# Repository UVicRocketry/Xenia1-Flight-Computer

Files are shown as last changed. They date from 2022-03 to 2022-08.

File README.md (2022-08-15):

# Xenia1-flight-Computer

## Requirements/Imports
To pip install all the necessary imports run
`$ pip install -r requirements.txt`
*Please Update requirements.txt with new imports if you add any*

## Style

- Class names: starting with Pascal Case (capital then camel)
- method: lower snake
- vars: lower snake
- private methods: \_\_ for private methods

Please document your code in the following format:

for classes:

```
  """
  Description of class

  ...

  Attributes
  ----------
  an_attribute(variable)
    Description:
      write description

  Methods
  -------
    Description:
      write description
     Parm:
      parm_name: write point of parameter

  """
```

## Setup and Installation

This system is designed to run on a raspberry pi zero W. To set up clone the repository and run `$ pip install -r requirements.txt`, this will install all necessary dependencies. 

## Design 

The flight computer has two purposes: to store, and to simulate. The system is designed to run on a raspberry pi 0 W running rasbian (Ubuntu ~10). Connected to the pi are multiple senors and devices. The sensor suite contains a adafruit BME280, adafruit LSM..., adafruit Adx..., adafruit ADS... all of which are connected to the pi using 1 I2C bus. A mirco stepper driver is used to control the airbrakes assembly's motor and feedback is given through a potentiometer which is fed into the analog to digital converter. A buzzer is connected to a single GPIO pin on the pi and give auditable feedback to the user. All other electrical components connected to the flight computer can be found in the KiCAD schematic in the source directory.

Due to the nature of embedded systems

Beep codes

## File structure

The Project is broken into two folders a source folder (src) and a sub sensors folders
```
> Xenia1-flight-computer
  > drag_data 
    > cda_no_airbrakes.csv

  > src
    > airbrakes.py
    > suborbit.py
    > rehearsal.py
    > main.py
    > rocketData.py
    > flight_computer.py

  > sensors
    > adx.py
    > bme.py
    > hx711.py
    > lsm.py
```

1. src/airbrakes.py

  Suborbit 

   Computes a the next value to set the airbrakes to position to. Also provides a simple interface for controlling the hardware that Airbrakes uses to  deploy the brakes. It does this through a kalman filter algorithm. Please look at the kalman filter algorithm connected    to the issue X1-AV-6 [](https://github.com/UVicRocketry/Xenia1-flight-Computer/issues/14)

2. src/suboribit.py

3. src/gpioReader.py

   This file reads all the data from the sensor and updates rocketData.

4. src/main.py

   Runs flight computer class

5. src/rocketData.py

   This class holds all the data of the rocket and has functions to manipulate the data.

## Flow of the Program

   <deprecated>
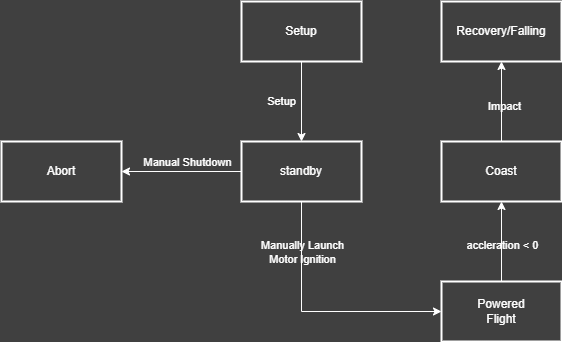
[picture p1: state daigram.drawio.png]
Main State Diagram


Sequence Flow of initial design. This was changed into a class containing different phases 

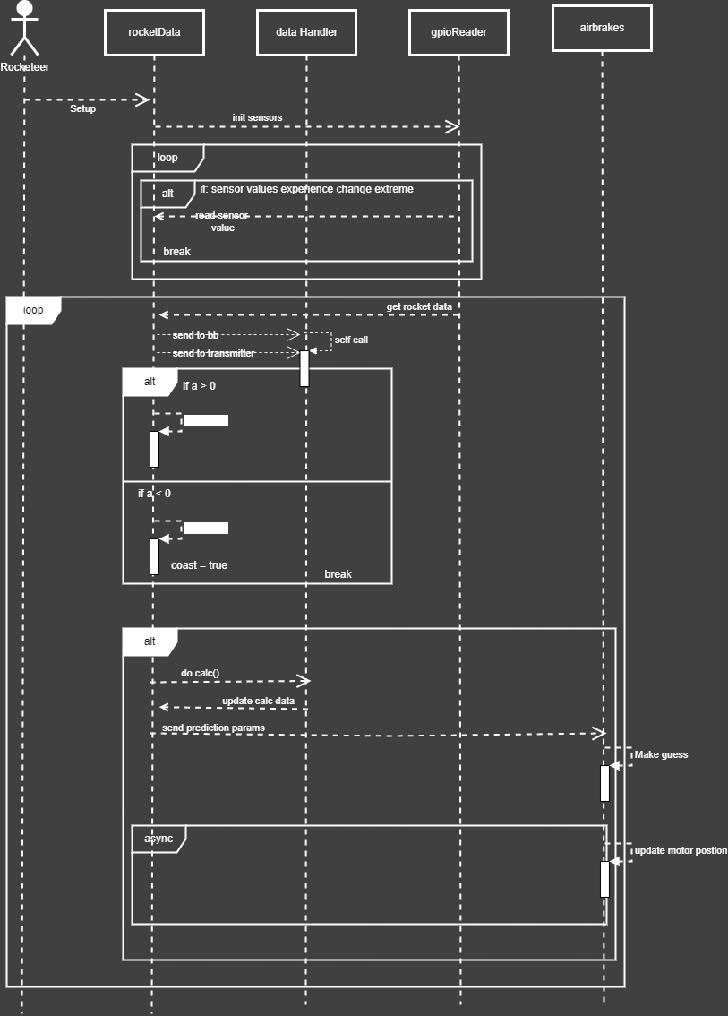
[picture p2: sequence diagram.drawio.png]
Sequence Diagram of main


## Air Brakes

The airbrakes assembly ...

For Xenia-1 we over spec'd our motor 

### Kalman Filter

As an suggestion from the MECH 400 report for airbrakes we explored the Kalman filter option for the predictive element of controlling airbrakes. A Kalman filter as shown in the diagram below predicts new state based on previous state. In the case of airbrakes this is a change in flap opening percentage determined by how the drag produced will impact the final altidute of the flight.   

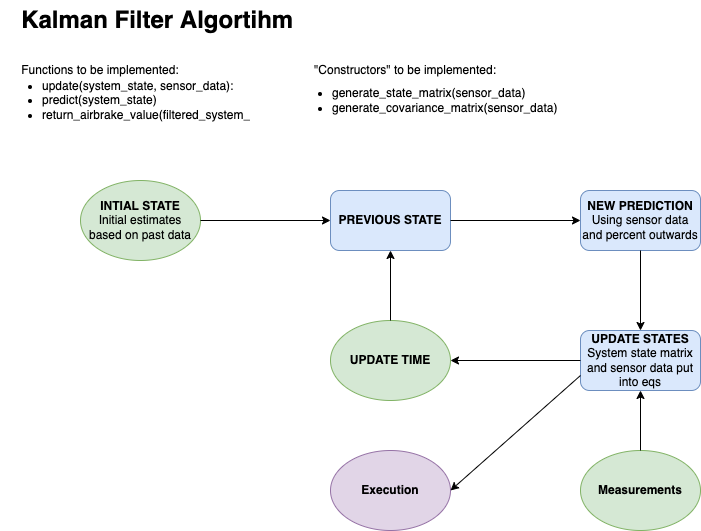
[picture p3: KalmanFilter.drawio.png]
Kalman Filter Image


### Suborbit

## Results and Reflection

After a almost nominal flight Xenia-1 was recovered with somewhat minimal data loss. See (link to post flight analysis) for a post flight analysis break down. Based on these results and barriers during development the following conclusions were made. _A raspberry pi is not a suitable processing unit for a rockets avionics system_. A raspberry pi runs an OS for more general purpose computing, what is needed is a device that only runs processes specific to its purpose. Another problem faced during development was the lack 

Developmentation:

This project should have been designed with proper requirements gathering from all subsystems and all core members involved. In addition a new development strategy was used in the middle of the development. This made the

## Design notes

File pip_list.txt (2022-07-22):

Package                          Version
-------------------------------- ---------
Adafruit-Blinka                  8.0.2
adafruit-circuitpython-ads1x15   2.2.15
adafruit-circuitpython-adxl34x   1.12.3
adafruit-circuitpython-bme280    2.6.13
adafruit-circuitpython-busdevice 5.1.10
adafruit-circuitpython-lsm9ds1   2.1.14
adafruit-circuitpython-typing    1.7.1
Adafruit-PlatformDetect          3.24.1
Adafruit-PureIO                  1.1.9
arandr                           0.1.10
astroid                          2.5.1
asttokens                        2.0.4
automationhat                    0.2.0
beautifulsoup4                   4.9.3
blinker                          1.4
blinkt                           0.1.2
buttonshim                       0.0.2
Cap1xxx                          0.1.3
certifi                          2020.6.20
chardet                          4.0.0
click                            7.1.2
colorama                         0.4.4
colorzero                        1.1
cryptography                     3.3.2
cupshelpers                      1.0
dbus-python                      1.2.16
distro                           1.5.0
docutils                         0.16
drumhat                          0.1.0
envirophat                       1.0.0
ExplorerHAT                      0.4.2
Flask                            1.1.2
fourletterphat                   0.1.0
gpio                             0.3.0
gpiozero                         1.6.2
html5lib                         1.1
idna                             2.10
isort                            5.6.4
itsdangerous                     1.1.0
jedi                             0.18.0
Jinja2                           2.11.3
lazy-object-proxy                0.0.0
logilab-common                   1.8.1
lxml                             4.6.3
machine                          0.0.1
MarkupSafe                       1.1.1
mccabe                           0.6.1
microdotphat                     0.2.1
mote                             0.0.4
motephat                         0.0.3
mypy                             0.812
mypy-extensions                  0.4.3
numpy                            1.19.5
oauthlib                         3.1.0
olefile                          0.46
pantilthat                       0.0.7
parso                            0.8.1
pexpect                          4.8.0
pgzero                           1.2
phatbeat                         0.1.1
pianohat                         0.1.0
piglow                           1.2.5
pigpio                           1.78
Pillow                           8.1.2
pip                              20.3.4
psutil                           5.8.0
pycairo                          1.16.2
pycrypto                         2.6.1
pycups                           2.0.1
pyftdi                           0.54.0
pygame                           1.9.6
Pygments                         2.7.1
PyGObject                        3.38.0
pyinotify                        0.9.6
PyJWT                            1.7.1
pylint                           2.7.2
pyOpenSSL                        20.0.1
pyserial                         3.5b0
pysmbc                           1.0.23
python-apt                       2.2.1
pyusb                            1.2.1
rainbowhat                       0.1.0
reportlab                        3.5.59
requests                         2.25.1
requests-oauthlib                1.0.0
responses                        0.12.1
roman                            2.0.0
rpi-ws281x                       4.3.4
RPi.GPIO                         0.7.0
RTIMULib                         7.2.1
scrollphat                       0.0.7
scrollphathd                     1.2.1
Send2Trash                       1.6.0b1
sense-hat                        2.2.0
setuptools                       52.0.0
simplejson                       3.17.2
six                              1.16.0
skywriter                        0.0.7
sn3218                           1.2.7
soupsieve                        2.2.1
spidev                           3.5
ssh-import-id                    5.10
sysv-ipc                         1.1.0
thonny                           3.3.14
toml                             0.10.1
touchphat                        0.0.1
twython                          3.8.2
typed-ast                        1.4.2
typing-extensions                3.7.4.3
unicornhathd                     0.0.4
urllib3                          1.26.5
webencodings                     0.5.1
Werkzeug                         1.0.1
wheel                            0.34.2
wrapt                            1.12.1

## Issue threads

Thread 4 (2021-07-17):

X1-AV-11 BME and IMU reading

jberryman566, 2021-07-17:
- reading data from sensors

klemie, 2022-02-17:
Needs broken up into smaller issues for each sensor. and have datasheets attached to the new issues

Closed 2022-03-01.

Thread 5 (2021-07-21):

X1-AV-10 Sending Data

jberryman566, 2021-07-21:
- Sending to air brakes  (encoder data )
- black box (Urt)
- ground station (antenna trans) -> in aprs package

The functions for this code can be found in dataHandler.py

klemie, 2022-02-17:
This is now a milestone can close this

Closed 2022-02-17.

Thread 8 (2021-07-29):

X1-AV-9 ADC research

klemie, 2021-07-29:
Research how these work for Rpi Zero W

klemie, 2022-02-17:
Feb 16th Update: I dont think Aila knows this is assigned to her. But this issue is to look into the ADC for the stepper driver.

Closed 2022-02-24.

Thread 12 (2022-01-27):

Wire flight computer

klemie, 2022-01-27:

klemie, 2022-02-17:
Feb 16th update:
@TechGal hasn't done this will do with Alex at the workshop

TechGal, 2022-03-24:
Step 1: mount electronics
step 2: wire (solid core)

apthornwell, 2022-04-02:
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
Followed wiring schematic to wire some things to a breadboard.

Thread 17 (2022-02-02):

X1-AV-5 Fix Holes on Avionics Bay Assembly

klemie, 2022-02-02:
Update the locations of the holes on the avionics bay assembly to accommodate current sensors.

jjderooy, 2022-02-19:
This is complete aside from the mounting for the camera which hasn't been chosen yet.

jjderooy, 2022-02-22:
[Camera](https://www.aliexpress.com/item/1005001597402383.html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) is now chosen and avionics bay holes are corrected.

Closed 2022-02-22.

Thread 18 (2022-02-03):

X1-AV-4 Convert to CSV

klemie, 2022-02-03:
Convert the following JSON object to a CVS:
```
{
  "timestamp": string,
  "bme": {
	  temperature: float,
	  humidity: float,
	  pressure: float
	  },
  "imu":{
	  acceleration: float,
	  magnetometer: float,
	  gyroscope: float,
	  temperature: float
  },
  "strain_gauges":{
	  "strain_one": float,
          "strain_two": float,
	  ....
	  "strain_twelve": float
  },
  "encoders": {
	  "position": float
  }
}
```
You can find more info here: http://142.104.84.19:8080/apps/drawio/9371

Add your solution to src/rocketData.py under the method convert_to_csv()

klemie, 2022-02-03:
This issue blocks sending data

klemie, 2022-02-17:
Feb 16th Update: Sydeny hasn't start yet. Will come to the workshop to get her started.

klemie, 2022-02-24:
Just working through it. But not much progress because of lack of python knowledge

Closed 2022-03-15.

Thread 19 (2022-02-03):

X1-AV-3 Making mocks for BME and IMU

klemie, 2022-02-03:
**Description**
- Mocks are need for all the sensors in order to test how our system reacts to weird flight data

**Acceptance Criteria**
- Create Mocks for IMU and BME
- Print random data using functions already created

**Linked issues**

klemie, 2022-02-17:
Feb 16th update: Met with Connor. Went through testing plan and learned how mocks work.

Closed 2022-03-08.

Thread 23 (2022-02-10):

X1-AV-12 HX711 reading

klemie, 2022-02-10:
Find the data sheet of the HX711 in this [](https://docs.google.com/document/d/1gTJJ3SIZ1-oAkT5Fk1SbSard9b0-FxJ6s4E3crWBEo4/edit) and see if there are any combatiable python libraries if not figure out how we would read the data.

klemie, 2022-02-17:
Feb 16th update: Charlie hasn't been able to get anything done yet. Needs data sheet to look at driver info

jjderooy, 2022-02-19:
This is the datasheet. It includes a C driver that could be rewritten in python if needed. [https://www.digikey.com/htmldatasheets/production/1836471/0/0/1/hx711.html](url)

klemie, 2022-02-24:
- Meet up with @TechGal tomorrow at 4pm

klemie, 2022-03-01:
https://github.com/UVicRocketry/Xenia1-flight-Computer/issues/27#issuecomment-1054649776

klemie, 2022-03-09:
[multi HX711 Arduino](https://github.com/shmulike/HX711-multi)

klemie, 2022-03-17:
mostly the framework is done. Having Troubles changing types. Just let python choose.

Having a hard time reading reading hex from the sensor.

klemie, 2022-03-17:
@PokeyOne will help figure out c conversion

jjderooy, 2022-04-22:
Finished in #56.

Closed 2022-04-22.

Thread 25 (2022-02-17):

X1-AV-13 Make wiring diagram for whole system

krislemie, 2022-02-17:
**Description**
- Create a writing diagram for the flight computer based off of previous diagrams

Previous Diagram: [diagram](https://app.diagrams.net/#G16KAys3ZIa_PrymFaww2CI59HlfeUq78S)
- Note this diagram is very out of date

**Acceptance Criteria**
- Updated Diagram KiCAD schematic uploaded to Xenia1-flight-computer

**Dev Note**
[Write why you decided to do specific wiring arrangement in Pull Request]

klemie, 2022-02-17:
Look at this diagram to see all the components https://drive.google.com/drive/u/0/folders/1lUKZYj5jFLF3oOM159mu564QdC9ljHMy

klemie, 2022-03-01:
Alex is making a diagram in KiCAD

TechGal, 2022-03-03:
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

TechGal, 2022-03-03:
Next steps: put into kicad. and figure out where other sensors go

klemie, 2022-03-17:
Finished 4 sensors in kicad

krislemie, 2022-03-21:
review:
- change Wires to labels
- Harnesses

TechGal, 2022-03-24:
Due by april 1st:

- [ ] Black box - USB connection (two pins Maybe DX and RX)
- [ ] ADC - addafruit 12bit analog to digtail converter (maybe 2 pins)
- [ ] Encoder - @TechGal

TechGal, 2022-05-31:
This last iteration looks really good! Having all the wires run where they will run on the rocket will be very helpful for wiring. If you could label each wire with it's use or protocol, that would be even more helpful. Also, dividing the page using a double line or something so it's very clear where the wiring diagram is and where the full schematic is. It would be really nice if you could edit the RPi schematic object and add the camera port at the bottom, to remove the ambiguity of having that port as it's own separate thing. You can also label the Raven4s with APO -> Drogue, and Main -> Main. These are on the recovery bulkhead, so off to the right of the rest of the schematic (if we look at this as the rocket lying sideways).

Good work, thanks for taking this on.

Closed 2022-06-16.

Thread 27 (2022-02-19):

X1-AV-15 HX711 Testing reading

klemie, 2022-02-19:
**Description**
- Talk to JJ and figure how we are going to read the data from his PCB to the flight computer.

**Acceptance Criteria**
- Software is written that knows how to receive and handle 12 different strain gauge values from 1 hdmi input
- Plan for how to wire HDMI cable to rpi is added to KiCAD schematic that @apthornwell is making in #25

**Dev Notes**

[Write notes on why you choose the wiring that you did. Explain how software works. Document in Pull request description]

cjsquires, 2022-02-28:
This library works for the HX711 (and is in python) https://github.com/gandalf15/HX711/
It the python file of the driver is rather large, but should work. The file also has all the validity checks included, and is very well documented.

If it turns out to be too much for the flight computer to handle, then we could also call the compiled c driver from python.

I can clarify anything that’s confusing to anyone (hopefully)

jjderooy, 2022-03-01:
I had a look at the python lib you linked. It looks pretty good but will need to be modified since we are  using multiple HX711s with a single clock line. Basically the way it works is the flight computer will pulse the clock line, and the HX711 will send data back on the data line. The lib you linked only allows one HX711 (ie one data line) per clock line.

Up to you whether you think it will be easier to modify the library or write your own. After reading through the code, there is a lot of extra error checking and functions which don't really apply to what we're doing like setting the output to kilograms and that sort of thing. Most of these libraries are designed to use HX711s for kitchen weigh scales which is why they have all those features.

Up to you whether you think it will be easier to modify the library or write your own. Alternatively, here is a [multi HX711 Arduino](https://github.com/shmulike/HX711-multi) library that you could convert to python.

TechGal, 2022-03-03:
Move to next sprint.
- converting c++ to python

jjderooy, 2022-04-22:
Finished in #56.

Closed 2022-04-22.

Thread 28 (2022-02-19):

X1-AV-16 Get data from Rpi camera

klemie, 2022-02-19:
**Description**
- The camera we will be using is a raspberry Pi camera look up its data sheet and see if it has a python library.
- Decide weather to save the video in rocketData.py, in a separate file.
- Make sure that it won't slow down our data transfer. If it does decouple it from

**Acceptance Criteria**
- Video is either saved to a video file (That can be sent to black box) or configured in the code and ready to be saved and able to be directly sent to backbox
- See how you would save the camera data to the py and if how python would send it

**Dev Notes**
[for assignee in PR]<write down your thought process when developing this issue>

**Linked issues**
 <If there are any related issues>
Blocked by #33 use this info from this issue to code this issue

TechGal, 2022-03-31:
Will be started later this week.

MaiaPys, 2022-04-01:
Basic video capture script was written but not yet tested due to connectivity issues. Will be tested as soon as possible.

TechGal, 2022-05-11:
@MaiaPys can you please send what you've been working on for the camera? We're hoping to bring together all the updates. Thanks!

Closed 2022-05-18.

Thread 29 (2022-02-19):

X1-AV-17 Write Issues for air brakes plan

klemie, 2022-02-19:
**Description**
Read old repo (python airbrakes), if you are confused on anything talk to conner ebert our team lead.
**Acceptance Criteria**
- Write new issues to break everything up project up into tasks
- Talk to @TechGal and @Kris to make sure they make sense to them

**Dev Notes**
[for assignee in PR]<write down your thought process when developing this issue>

**Linked issues**

klemie, 2022-03-09:
Set a date for the meeting

klemie, 2022-03-10:
Add issues to https://github.com/UVicRocketry/Xenia1-flight-Computer/milestone/3

PokeyOne, 2022-03-17:
# Mateo's Dev Notes

This comment is a work in progress; I'm just writing some notes in a github comment as I work.

Here is a diagram from the "MECH400_FinalReport_Group13.pdf" docment available on GitHub
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

And here is another diagram from the "software in-the-loop testing" section of the same document. Figure 28: "Simulink Model of AACS Control System and Flight Dynamics"
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

*I'm just going to edit this comment as I work through components that this can be broken down into*. After discussing tonight, issues can be created and branches, and then get programming.

## Components/Tasks
Here's a sorta workflow type thing on what needs to be developed
```mermaid
flowchart LR
    Issues[Create Issues] --> sensor[Sensor Data Retrieval in One Object/Struct]
    Issues --> Kalman
    Kalman --> Drag[Drag Optimizer]
    Issues --> Output[What does output look like]
    sensor --> Kalman
    Drag --> Motor
    Kalman -- error data --> Motor[Motor Controller Convert Error into steps]
    Motor --> Output
    sensor --> State["Determine when system is active [1]"]
    State --> Motor
```
[1] See "5.2.6 Active Control Flight Envelope" section of the report.

In the first diagram of this comment, they mention the "State Observer" is where the Kalman stuff would be happening.

**Here are how I'm thinking of breaking this up**:
- [ ] Transform sensor input from raw data to interpretable numbers
- [ ] Make kalman take the input data and output error data.
- [ ] Drag Optimizer (Not sure what this will involve)
- [ ] Convert drag-op and kaman values into flap angles and motor steps
- [ ] Output data back to motor and self.
- [ ] control when system active/not

All stages should include testing of that stage.

## What I'm not Sure on
- Not sure the scope of the "air brakes" plan. Seems like this is less air brakes, and more just flight controller.
- What the drag optimizer 100% does.
- How much of that report we are following exactly and how much is changed in recent development.
- The flight dynamics section of the first graph.
- How are we testing stuff.

klemie, 2022-03-17:
Discuss at meeting

PokeyOne, 2022-03-23:
## Summary of results from meeting on this issue

There is a more detailed summary of the Airbrakes meeting on the Discord under AEROSTRUCTURE in the `# | airbrakes |` channel.

I will be translating a Matlab script we have into python and we will see how well it can predict final altitude of the rocket at different points in flight. If that script works, we may just use that script instead of a full Kalman filter to determine how much we need to deploy airbrakes.

TechGal, 2022-03-24:
other predictive options: TinyML

Closed 2022-04-07.

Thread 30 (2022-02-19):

X1-AV-18 Get[value] Airbrakes Stepper Potentiometer/Encoder

klemie, 2022-02-19:
**Description**
- Get the potentiometer values from the airbrakes and store in rocketData object

**Acceptance Criteria**
- self._data is updated in rocketData.py with the new encoder value (make sure to test this with print statements show screenshots in PR)

**Dev Notes**
[for assignee in PR]<write down your thought process when developing this issue>

jjderooy, 2022-02-19:
The device is just a potentiometer. As you spin it the ADC it is connected to will send a reading of 0-1023 (most likely) to the flight computer GPIO pins. It's just like the VEX potentiometers we used in engr120 if you remember those.

jjderooy, 2022-04-07:
Hopefully mostly fixed in #53 . This at least lays the groundwork for it, though main will still need to actually put the data in rocketData from my understanding. None of the other data have integration with main yet so hopefully this is sufficient?

Closed 2022-05-17.

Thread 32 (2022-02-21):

X1-AV---

TechGal, 2022-02-21:
Design a camera mount to hold a camera against the fuselage of the rocket, without requiring internal access to insert.

jjderooy, 2022-02-22:
I'm not sure how you are organizing things but since this is a mech project rather than software would it make more sense for this to go on openproject?

MorganStuyt, 2022-02-23:
@jjderooy & @TechGal Yes, this task is created in openproject.

jjderooy, 2022-02-23:
Closing this with recommendation from Kris

Closed 2022-02-23.

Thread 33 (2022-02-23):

X1-AV-20 Camera Video storage

klemie, 2022-02-23:
**Description**
- Decide where the camera data will be stored
- decide the rate at the which
- location where it will be stored
- What medium we will be communicating it

**Acceptance Criteria**
- write smaller issues
- decide if we need additional hardware
- what software is needed

**Dev Notes**
[for assignee]<write down your thought process when developing this issue>

**Linked issues**
 <If there are any related issues>

<Add to milestone>
blocked by #28

klemie, 2022-02-24:
- Find the library for python specific camera.
- look on raspberry pi website.
- look at the sensor

Closed 2022-03-21.

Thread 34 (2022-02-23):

X1-AV-21 PID Algorithm

klemie, 2022-02-23:
**Description**
- Create a PID controller to set the kalman output to the set output of the stepper position to
- This is the Kalman filter @TechGal dont think this issue is necessary
(This might be over complicating it @TechGal )

**Acceptance Criteria**
 <Write specifically what is need for this issue to be completed>
- output of PID give a result in an exceptionable range

**Dev Notes**
[for assignee]<write down your thought process when developing this issue>

**Linked issues**
 <If there are any related issues>

jjderooy, 2022-02-25:
I wouldn't bother with a PID controller for the stepper. The flaps don't need to deploy super fast and don't have much inertia either. The nice thing with steppers is that there is no overshoot. I'll close this in a bit unless there was a specific reason you (@klemie/@TechGal) wanted PID that I've missed.

Closed 2022-02-26.

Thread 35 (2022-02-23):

X1-AV-22 Write Recieving data (code + documentation)

klemie, 2022-02-23:
**Description**
- Create pass/fail requirements
- Create script to start the test
- Create test with simulated flight data set and actual sensors

**Acceptance Criteria**
- Tests are verbose and handle all sensors

**Dev Notes**
[for assignee]<write down your thought process when developing this issue>

**Linked issues**
#19

TechGal, 2022-03-31:
Writing a test for the tests, to make sure they work. A sample test.

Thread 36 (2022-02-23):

X1-AV-23 Build simulation flight data set

klemie, 2022-02-23:
# Description
 <Describe what the feature or bug that need to be resolved>
Look at old flight data and create a set of data to be used in testing the system

# Acceptance Criteria

- [ ]  Simulation set should have all sensors, and a time stamp. Follow the same structure shown in Rocketdata.py
- [ ]  simulation set follows the same models an actaul flight
- [ ]  Ask @MorganStuyt  for more info
# Dev Notes
[for assignee]<write down your thought process when developing this issue>

**Linked issues**
Blocks #35

TechGal, 2022-06-09:
data may be weird. Temp readings weird

Closed 2022-11-17.

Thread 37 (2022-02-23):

X1-AV-24 Transmitter Processing

klemie, 2022-02-23:
**Description**
- Convert data into a csv like structure to be sent to the transmitter
- ex: `imu['Imu_t'], imu['imu_h'], imu['imu_p], ..., bme['bme_t], ...`
- Edit `convert_antenna_format` method in rocketData.py

**Acceptance Criteria**
- Formats all of `self._data` into a long array separated by commas similar to #41
- has a maximum of 200 characters -- figure out what values are most import to send to the ground
- Most important parameters will be from BME280, and linear accelleration/velocity from IMU, these will help us develop a picture of the rocket's flight on the ground during flight, and better estimate recovery location.

**Dev Notes**
[for assignee]<write down your thought process when developing this issue in the PR>

**Linked issues**
blocked by #43
#41

Closed 2022-05-11.

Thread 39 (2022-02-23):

X1-AV-25 Airbrakes Stepper/A4988 Control

klemie, 2022-02-23:
**Description**
- @jjderooy

**Acceptance Criteria**
 <Write specifically what is need for this issue to be completed>

**Dev Notes**
[for assignee]<write down your thought process when developing this issue>

**Linked issues**
 <If there are any related issues>

<Add to milestone>

jjderooy, 2022-02-26:
What do you mean by stepper data? They are open loop so there is no feedback. The feedback we get is from the encoder (potentiometer) which already has an issue: #30

jjderooy, 2022-02-26:
Ah gotcha. Stepper control is handled by the A4988s. Logan and I wrote some code for hybrid test stand steppers that can be used. I'll see if I can make a PR for it.

jjderooy, 2022-02-27:
@krislemie  Where should the code for controlling the stepper via a4988s go? It could go either in `main.py` or in `airbrakes.py`. The description for `airbrakes.py` is:
> Computes a the next value to set the airbrakes to position to. It does this through a kalman filter algorithm. Please look at the kalman filter algorithm connected to the issue X1-AV-6

I could update this to include the physical control as well.

Lmk what you think and I'll make a PR.

klemie, 2022-02-27:
Everything should be decoupled from `main.py` so it should be in airbrakes.py a PR would be good

jjderooy, 2022-03-08:
Alright @klemie I'm done with my branch, but I can't test the code until the flight computer is assembled. Would you like a PR anyways?

Closed 2022-03-18.

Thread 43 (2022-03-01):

X1-AV-27 Update rocketData

klemie, 2022-03-01:
**Description**
- Reformate rocketData in rocketData.py to be the actual values from the senors
- For example the IMU is actually called a LSM and has different values then we thought like three

Heres an example:
_Current BME_
```py
   'bme': {
                'yaw': float,
                'pitch': float,
                'roll': float,
                'linear_acceleration': float,
                'linear_velocity': float
    }
```
_More Correct BME_
```py
   'bme': {
                'Temperature': float,
                'Humidity': float,
                'Pressure': float
    }
```
^ look at datasheet for more accurate values.
**Acceptance Criteria**
- Change `self._data` to reflect what the sensors values actually are on the data sheets which you can find in the sending data milestone or datasheets in NC under UVR++ -> Rockets -> Xenia-1 -> Avionics -> Datasheets
- Change Strain Gauges to a list of twelve instead of a dict
- update getters and setter accordingly

**Dev Notes**
[for assignee]<write down your thought process when developing this issue on PR>

**Linked issues**
 <If there are any related issues>

<Add to milestone>

klemie, 2022-03-17:
Wrote down what there suppose to be hasnt started coding yet

Closed 2022-05-17.

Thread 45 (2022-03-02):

X1-AV-28 Threading

klemie, 2022-03-02:
# Description
Have individual threads for Air brakes, data handling. This will decouple the processes from one another and allow air brakes to work paralleled with sending and receiving data.

_Possible problems:_

1. Sending thread could be sending repeat if receiving thread isn't fast enough
[Possible solution]
- Keep sending and receiving data in one thread. Start by receiving then send once all data is collected (I suggest this one)
- Buffer sending thread to only send until receiving thread has collected all the data.
2. air brakes doesn't get updated sensor values in time. Could put the brakes in the wrong position.

Note: use **https://docs.python.org/3/library/threading.html**

1. Initialize threads in `initialize()` phase.
- use `_thread.start_new_thread()`, Takes a function as parameter function this will be the code that the thread executes.
**create 2 threads:**
- one thread for moving air brakes
- one thread for everything else
2. In the `coast_flight` calculate initial suborbit guess
3. In the `coast_flight` phase send airbrakes thread(AB) percentage value and move the motor
- AB thread will move the motor then send a finished flag to the main thread
- Once the main thread receives finished flag it will suborbit again and send that
4.

# Acceptance Criteria
- [ ] Threads handle main processes, Air brakes
- [ ] Checks are made to make sure all data has been received
- [ ] Make sure air brakes thread receives data from data handling thread

**Dev Notes**
[for assignee in PR]<write down your thought process when developing this issue>

**Linked issues**
#22

klemie, 2022-06-02:
Monday: 6pm, threading meeting

TechGal, 2022-06-09:
Moter needs to know length of time on sleep, to determine when and if it should move. Wont need threading, rework airbrakes slighty to get rid of sleep

Closed 2022-06-09.

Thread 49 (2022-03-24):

X1-AV-31 Convert Sub-Orbit from Matlab to Python

ebert-c, 2022-03-24:
**Description**
Sub-Orbit is a matlab program that will allow us to estimate our trajectory in real time.
We will be varying our drag utilizing the airbrakes to hit our target altitude.

We need to convert the Matlab program into Python and integrate it into the flight computer.
It will need to acquire sensor data and use that data to solve for the needed drag coefficient to achieve target altitude.

**Acceptance Criteria**
The Sub-Orbit program is converted to Python from Matlab and is able to receive sensor data from flight computer and output a drag coefficient that is needed to hit target altitude.

**Dev Notes**
[for assignee]<write down your thought process when developing this issue>

**Linked issues**
 <If there are any related issues>

<Add to milestone>

PokeyOne, 2022-04-21:
https://github.com/UVicRocketry/Suborbit-Prediction-Script

PokeyOne, 2022-05-12:
Currently there are three main components of this that need to be done: The atmosphere function, the power phase, and the coast phase.

Currently the atmosphere component is done, the power phase is almost done, and should be done tonight. The coast phase will be very similar to the power phase so this is getting very close to the matlab script.

PokeyOne, 2022-05-12:
Next steps after this is done:
- Test on pi
- Is it fast enough?
- How are we integrating it with the rest?

PokeyOne, 2022-05-18:
Quick update on this for May 18 2022.

I think this is probably closable?

This issue seems to be mostly the conversion of the script.

The script is fully converted over at <https://github.com/UVicRocketry/Suborbit-Prediction-Script> , and most of the stuff left to complete is optimization and evaluation.

Closed 2022-11-17.

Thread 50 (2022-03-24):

X1-AV-32: Control Stepper Motors Based on Needed Drag Coefficient

ebert-c, 2022-03-24:
**Description**
Given a needed drag coefficient, open the flaps controlled by the stepper motor to the position needed to achieve said drag.
A converter between drag coefficient and stepper motor position will be provided by Flight Dynamics.

**Acceptance Criteria**
When given a drag coefficient input, the system can cause the stepper motor to open the flaps to the position that provides that drag coefficient.

**Dev Notes**
[for assignee]<write down your thought process when developing this issue>

**Linked issues**
 <If there are any related issues>

<Add to milestone>

TechGal, 2022-06-09:
Follow up with claire.

TechGal, 2022-06-09:
Need updated drag coefficient list from claire.

Closed 2022-11-17.

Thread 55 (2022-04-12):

X1-AV-33 Refactor HX711 driver for testing

klemie, 2022-04-12:
**Description**
@cjsquires started #54 however this needs to be finished for testing. There were a lot of questions in that code so make sure to follow the reference Arduino driver word closely
**Acceptance Criteria**
- Can read 12 HX711s

**Dev Notes**
[for assignee]<write down your thought process when developing this issue>

**Linked issues**
 <If there are any related issues>

<Add to milestone>

jjderooy, 2022-04-22:
Nothing really needs to be refactored with the driver in #56. It does need to be tested with 12 HX711s on the PCB to be fully sure it works, but I have done quite a bit of testing with breakout boards and it does work fine with 2. I'll close this unless there were other things specifically you wanted to test.

Closed 2022-05-18.

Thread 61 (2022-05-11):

Print new AV bay

TechGal, 2022-05-11:
Description

Acceptance Criteria

Dev Notes
[for assignee]

Linked issues

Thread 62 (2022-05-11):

Wire electronics on AV bay

TechGal, 2022-05-11:
Description

Acceptance Criteria

Dev Notes
[for assignee]

Linked issues

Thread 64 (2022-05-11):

Test programmed RPi to ensure no egregious faults

TechGal, 2022-05-11:
Description

Acceptance Criteria

Dev Notes
[for assignee]

Linked issues

jjderooy, 2022-05-15:
@TechGal this needs a description. After talking with Jenny she has no idea what to do because the issue is so vague. Thanks.

TechGal, 2022-05-17:
Description has been updated, @jjderooy @j7uu

klemie, 2022-05-18:
[@krislemie ]Need an Elec student to wire everything and get everything ready for @j7uu

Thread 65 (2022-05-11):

Check for low-noise filter on ground station

TechGal, 2022-05-11:
Description

Acceptance Criteria

Dev Notes
[for assignee]

Linked issues

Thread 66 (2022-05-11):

Determine gain of transmitting antenna

TechGal, 2022-05-11:
Description

Acceptance Criteria

Dev Notes
[for assignee]

Linked issues

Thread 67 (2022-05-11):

Make feedline for antenna

TechGal, 2022-05-11:
Description

Acceptance Criteria

Dev Notes
[for assignee]

Linked issues

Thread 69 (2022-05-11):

Test ground station with antenna using transmitter

TechGal, 2022-05-11:
Description

Acceptance Criteria

Dev Notes
[for assignee]

Linked issues

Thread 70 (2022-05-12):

X1-AV-34 Test Suborbit script on Pi

krislemie, 2022-05-12:
# Description

Test the speed at which the simulation finish. Test the simulation on 1 thread with another tread running.

## Acceptance Criteria
 <Write specifically what is need for this issue to be completed>

- [x] Speed at which the program runs on the pi is documented
- [ ] How many threads can be ran while program is running
- [ ] Conclusions are made to weather this is a good option for predicting.

# Dev Notes

## From Mateo

***Speed?*** Currently 0.4s

***Thread count?*** This is technically how ever many the OS can manage in memory. But realistically just depends on what else we are running.

***Is it right?*** This needs to be discussed. See comments below.

# Linked Issues

- Over on the script's repo: UVicRocketry/Suborbit-Prediction-Script#4  This has optimization

<Add to milestone>

jjderooy, 2022-05-17:
@PokeyOne can you give an update on where things are at with the optimization you've done?

PokeyOne, 2022-05-17:
The optimization I have done was in UVicRocketry/Suborbit-Prediction-Script#4

This took the execution time on the PI from 54s to about 0.4s

This was on the pi while @jjderooy was doing some very light testing on the pi, and the time does not include loading csv data and sorting the data. The load time shouldn't be included anyway though because it can be done once while the rocket is on the ground, and takes just a few seconds anyway.

The only other thing that I wanted to try off the top of my head was to make the `atmosphere` function inside the script just a LUT to see if that would be faster.

## Is this the right option?

There are a couple factors in whether this is the best option -- mainly accuracy and speed. As far as speed, I think it is reasonable ish. 0.4s ok. It will also take less time as it gets higher, because there is less to predict. I could also make it less precise, but I did already do that. I am hoping that this gets at least a little bit less as things go. Now, in terms of accuracy, it's a bit harder to tell. Currently the script is estimating roughly 12700 ft with full airbrakes and 14400 ft with no airbrakes. I do still need to get exact final mass data and the drag coefficient data will need to be updated with the latest changes to the fins. This is a little bit higher that what ASTOS is saying, but who knows really.

PokeyOne, 2022-05-17:
Also @klemie I updated some of the information in the issue if that is alright. And changed the formatting a little bit if that is alright. I was thinking it could make sense for the headings to be headings in issues, and for the acceptance criteria to be a check list.

Closed 2022-11-17.

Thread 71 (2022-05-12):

X1-AV-35 Python multi threading

krislemie, 2022-05-12:
**Description**
Investigate how to thread in python and write documentation on how to do it.
**Acceptance Criteria**
-
**Dev Notes**
[for assignee]<write down your thought process when developing this issue>

**Linked issues**
 <If there are any related issues>

<Add to milestone>

Closed 2022-05-18.

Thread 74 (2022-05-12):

X1-AV-38 Add HX711 to gpioReader

klemie, 2022-05-12:
**Description**
Use the driver (HX711Multi.py) to get 12 input strain readings put the function in gpioReader

**Acceptance Criteria**
- rocketData its updated with the strain data
- uploaded to pi and tested with testing rig in the rocket room ask @jjderooy or @krislemie how to set it up

**Dev Notes**
[for assignee]<write down your thought process when developing this issue>

**Linked issues**
#56

<Add to milestone>

jjderooy, 2022-05-16:
More context: create an instance of the HX711Multi class and pass it a GPIO pin for the clock, and a list of 12 GPIO pins for data. Then use the build in methods like tare(), isReady() and read() to read strain data from the sensors. There is lots of documentation at the top of the HX711Multi.py file.

krislemie, 2022-05-16:
> More context: create an instance of the HX711Multi class and pass it a GPIO pin for the clock, and a list of 12 GPIO pins for data. Then use the build in methods like tare(), isReady() and read() to read strain data from the sensors. There is lots of documentation at the top of the HX711Multi.py file.

Thanks JJ!

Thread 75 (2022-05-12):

X1-AV-39 Pass Initial values into airbrakes

klemie, 2022-05-12:
**Description**
Initial values are needed inorder to create a prediction.

**Acceptance Criteria**
 <Write specifically what is need for this issue to be completed>

**Dev Notes**
[for assignee]<write down your thought process when developing this issue>

**Linked issues**
 <If there are any related issues>

<Add to milestone>

jjderooy, 2022-05-17:
@PokeyOne is this required for suborbit as it is written currently?

PokeyOne, 2022-05-17:
@klemie What are initial values?

PokeyOne, 2022-05-17:
I think I kinda understand this. There will be some values that the script will need, such as launch altitude. During flight it will also need current altitude, velocity, and acceleration if available. If some of those values are not available directly, using some sort of estimate may be viable. There may be some things that could be done with a temperature and pressure reading on the ground, but that is not currently how it is written.

In summary:

Initial values:
- [ ] launch altitude

During flight
- [ ] altitude
- [ ] velocity
- [ ] acceleration

klemie, 2022-05-18:
I need to fill out this issue better

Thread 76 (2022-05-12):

X1-AV-40 Calc altitude

klemie, 2022-05-12:
**Description**
There are about 3 different ways we can calculate altitude with the sensor data we have. We want to calculate current altitude in those three different ways compare them against eachother and send the result to airbrakes.

create a file called calculations.py and put these 3 calculation in there.
**Acceptance Criteria**

- [ ] multiple calculations of altitude are made
- [ ] a method to compare the calculated values is decided.
- [ ] Error handling checking if compare values are to different

**Dev Notes**
[for assignee]<write down your thought process when developing this issue>

**Linked issues**
 <If there are any related issues>

<Add to milestone>

jjderooy, 2022-05-16:
What sensors are available for calculating altitude?

Closed 2022-07-07.

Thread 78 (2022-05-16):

X1-AV-41 format rocketdata to transmitter state

krislemie, 2022-05-16:
# Description
Work with @TechGal to hack the message for the transmitter. Once figured out how to access the message take the formatted data from RocketData.convert_to_csv_string and format the data to a string and set the message value in the transmitter.

# Acceptance Criteria
 <Write specifically what is need for this issue to be completed>

- [ ] Figure out how to Hack the message field of the transmitter
- [ ] Create a case in csv string function in rocketdata to create a string with only the most import sensor data Char limit of 200c. Do 4 sig figs
- [ ] Write a function to update text field (writtin in send data)
- [ ] Test with actual transmitter to make sure field sends

# Dev Notes
[for assignee]<write down your thought process when developing this issue>

# Linked issues
 <If there are any related issues>
Similar to #37
<Add to milestone>

jjderooy, 2022-05-16:
Can you give some more context of how the transmitter connects? Name of transmitter, and libraries it uses that sort of thing? @TechGal any parameters we need to know about the antenna like character limits, packet frequency etc?

krislemie, 2022-05-16:
char limit is 200 but thats all I know

TechGal, 2022-05-17:
We're using the BigRedBee 70cm APRS [transmitter](https://shop.bigredbee.com/products/70cm-100mw-gps-aprs-transmitter). This transmitter uses a microcontroller which is initially programmed on a Windows computer, including a message which is sent to the ground with the automated GPS data and timestamp. The thing that needs to be determine is whether or not we can use the exposed UART interface to send a new message once / second (the recommended transmission speed). There are some programmers available, and I imagine there are some libraries too, for this microcontroller, but as this specific board is only used in a specific niche, I haven't found any tutorials explicitly discussing this board.

krislemie, 2022-05-19:
150c aprs package. Choose key values from rocketData to send.

krislemie, 2022-05-19:
we should figure out together in CDR

Closed 2022-06-30.

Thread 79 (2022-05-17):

X1-AV-42 add Null checks

klemie, 2022-05-17:
**Description**
For all sensor, any missed value is `null`. Use the last saved value for calculations.

**Acceptance Criteria**
- null checks are added to all sensors read in gpioReader
- `convert_to_cvs_string` in rocketData is updated to send null in the string
- `send_all_data` in dataHandler  is updated to save null properly

**Dev Notes**
[for assignee]<write down your thought process when developing this issue>

**Linked issues**
 <If there are any related issues>

<Add to milestone>

jjderooy, 2022-05-17:
Are you sure writing null is the best option for the data logging? I'm just thinking for when we analyze the data afterwards with matplotlib or excel its gonna be a pain to remove all the nulls. Would it be better to just copy the previous value again instead of null?

PokeyOne, 2022-05-18:
I remember the discussion on this last week, and thinking about it more I think it may actually make more sense to log the previous value.

I think the main argument for logging null would be to preserve the information that we weren't getting anything at that point, but this probably isn't all the important. If we look at the logs after and there is a streak of the exact same value to the 5th decimal place for half the flight we'll be able to tell if nothing was changing. It would also just simplify all the logic and reduce errors within the program. If we just have one variable that stores the previous value then there is one source of truth that is never null. If we start messing with null then we are going to have to check for null on every singe equation and it will get messy real quick.

Also it would just make things easier like JJ said.

Another option would be to just put an empty cell. I know people were saying would make it harder to read last week, but I don't think the CSV is really meant to be read by a human anyway. Most of the time if someone is looking at the data it should just be in some sort of software like excel. I still think I prefer having the previous value over an empty cell, but personally I think an empty cell is better than just writing `null`

Writing null can also be a bit misleading, because it makes it seem like we don't have data. We do have data. It just hasn't been updated that particular cycle.

j7uu, 2022-06-09:
Notes/Discussion From Avionics Meet (2022-06-08)
- Could use last value of the sensor for x amount of time (then enter timeout and use generic value)
- Discussed the merits and pitfalls of using old flight data for generic values (values based on time, values from comparing current sensors to old data, etc)
- Try catch all of main????????

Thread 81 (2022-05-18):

X1-AV-43 Update rocketData with sensor values

klemie, 2022-05-18:
# Description
Currently code has been written to read the sensor data from the IMU and LSM  into print statements. We need to change that to updating a rocketdata instance in main.

1. to do this we will update `__readBME280` and `__readLSM9DS1` by changing the print statements to a single return statement of an object that resembles what the print statements looked like.
eg:
```
print("Temperature: %0.1f C" % self.__bme280.temperature)
print("Humidity: %0.1f %%" % self.__bme280.humidity)
print("Pressure: %0.1f hPa" % self.__bme280.pressure)
```
->
```
return {
     't': self.__bme280.temperature
     ....
}
```
make sure to write fullnames for object keys

2. Create a public varaible of type RocketData (import rocketdata add initialize a new instance)

3. A public function will have to be made to return all updated sensor values. This function will call `__readBme` and `__readLsm` update the public rocketdata variable with the Bme and lsm values

---

These imports were accidentally deleted please add back to the top of gpioReader.
```
import board
import adafruit_lsm9ds1
from adafruit_bme280 import basic as adafruit_bme280
```
Also add imports to requirements.txt (board, adafruit_lsm9ds1, adafruit_bme280 )

---

test your code by running the code with the Mocks and printing out the state of call the public function (should return a rocketdata object). Maybe try running print statement in a for loop in main. Merged version of code will not include this testing code.

# Acceptance Criteria

- [ ]   imports are added in requirement.txt and to the top of gpioReader
- [ ] Screenshot of test results in PR
- [ ] __readBME & __readLSM are change to return objects
- [ ] A public function is created that update a public attribute of type rocketData with the values from `__readBME` & `readLSm`
# Dev Notes
[for assignee]<write down your thought process when developing this issue>

**Linked issues**
 <If there are any related issues>

<Add to milestone>

Closed 2022-06-05.

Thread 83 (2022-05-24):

X1-AV-50 Redo Sensor power Calculation

klemie, 2022-05-24:
# Description
 <Describe what the feature or bug that need to be resolved>
 <Description of the big component that encompasses the issue working on>
 <Depencies, ex. libraries, sensors, hardware, small parts of code youhave to work on>
 <ow to do the things>

Calculations with for sensors are done correctly and checked by other members

# Acceptance Criteria
 <Write specifically what is need for this issue to be completed>

- [x] Power Calculation include all up to date sensor
- [x] Confirm if we have enough power to last +6hr
- [x] Update documentation
- [x] Choose lipos or 9V

# Dev Notes
[for assignee]<write down your thought process when developing this issue>

# Linked issues
 <If there are any related issues>

<Add to milestone>

Closed 2022-06-29.

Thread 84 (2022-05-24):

X1-AV-51 Choose GoNoGo indicator

klemie, 2022-05-24:
# Description
 <Describe what the feature or bug that need to be resolved>
 <Description of the big component that encompasses the issue working on>
 <Depencies, ex. libraries, sensors, hardware, small parts of code youhave to work on>
 <ow to do the things>
 NOTE: if you import anything new add it to the list in `requirements.txt`

Choose a sensor indicator and have a diagram for start up sequence that will trigger the indicator

# Acceptance Criteria
 <Write specifically what is need for this issue to be completed>

- [ ] Choose an indicator. LED vs. Buzzer?
- [ ] Update CAD with indicator
- [ ] Create a flow diagram for the startup sequence
- [ ] Write follow up ticket for software implementation

# Dev Notes
[for assignee]<write down your thought process when developing this issue>

# Linked issues
 <If there are any related issues>

<Add to milestone>

Closed 2022-06-30.

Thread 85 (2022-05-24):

X1-AV-53 Change stepper driver for airbrakes

klemie, 2022-05-24:
# Description

Spec new more reliable stepper driver for airbrakes. @Devon-H knows the right one

# Acceptance Criteria

- [x] Integrate new sensor in cad
- [ ] Learn how to control it with python
- [ ] Implement into `src/airbrakes.py`
- [ ] Test that it works

# Dev Notes

# Linked issues

Devon-H, 2022-05-24:
The stepper motor driver in question is the DRV8825. Here's an amazon [link](https://www.amazon.ca/Baluue-Stepper-Compatible-StepStick-Printer/dp/B08PV6JTK7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) for reference

PokeyOne, 2022-06-29:
I just got assigned to this, but this may or may not already be finished. I know for a fact that I already updated the schematic, but I haven't looked at the code. I'll take a look later today.

If it is already updated, I will still want to test that it works before closing this issue.

Closed 2022-11-17.

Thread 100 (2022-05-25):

X1-AV-58 Velocity Calculations

krislemie, 2022-05-25:
# Description
 <Describe what the feature or bug that need to be resolved>
 <Description of the big component that encompasses the issue working on>
 <Depencies, ex. libraries, sensors, hardware, small parts of code youhave to work on>
 <ow to do the things>
 NOTE: if you import anything new add it to the list in `requirements.txt`

Take the calculated values from #76 and calculate velocities.

Create more functions in `datahandler.py` to calculate multiple velocity using different equations.

# Acceptance Criteria
 <Write specifically what is need for this issue to be completed>

- [ ] Create a list of equations to be used
- [ ] Create corresponding functions to equations
- [ ] Update class documentation explaining what params are need and what equation was used for each function
- [ ] Velocity is calculated

# Dev Notes
[for assignee]<write down your thought process when developing this issue>

# Linked issues
 <If there are any related issues>
blocked by #76
<Add to milestone>

Closed 2022-07-07.

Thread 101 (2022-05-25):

X1-AV-59 Object for storing calculated values [needs AC]

krislemie, 2022-05-25:
# Description
 <Describe what the feature or bug that need to be resolved>
 <Description of the big component that encompasses the issue working on>
 <Depencies, ex. libraries, sensors, hardware, small parts of code youhave to work on>
 <ow to do the things>
 NOTE: if you import anything new add it to the list in `requirements.txt`

Determine weather to create a class to that inherits rocket data properties and stores the calculated attributes or just add on to rocketData.

This object should have altitude, velocity, and acceleration at a specific point in time.

# Acceptance Criteria
 <Write specifically what is need for this issue to be completed>
- [ ]

# Dev Notes
[for assignee]<write down your thought process when developing this issue>

# Linked issues
 <If there are any related issues>

<Add to milestone>

Closed 2022-06-30.

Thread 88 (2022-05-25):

X1-AV-56 standardize apogee prediction and startup

krislemie, 2022-05-25:
# Description
 <Describe what the feature or bug that need to be resolved>
 <Description of the big component that encompasses the issue working on>
 <Depencies, ex. libraries, sensors, hardware, small parts of code you have to work on>
We have a couple different systems on the rocket that need to know apogee and starting launch. Based on the available sensors we need to create a universal way throughout the rocket to know when the launch has happened, and when the rocket has reached apogee.

# Acceptance Criteria
 <Write specifically what is need for this issue to be completed>

- [ ] Gather a list of sensor values available in all three systems (black berry jam, magpi, flight computer) you will have to talk to @cristyro & @Gordon-928 for details.
- [ ] Figure out what sensor values will dictate a launch
- [ ] Create function in `dataHadler.py` to return true when launch is detected
- [ ] Figure out what value will dictate of apogee
- [ ] Create function in `dataHadler.py` to return true when apogee is detected
- [ ] Work with @cristyro & @Gordon-928 to make C++ versions

# Dev Notes
[for assignee]<write down your thought process when developing this issue>

# Linked issues
 <If there are any related issues>

<Add to milestone>

Closed 2022-06-30.

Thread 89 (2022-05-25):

X1-AV-57 Update main.py

krislemie, 2022-05-25:
# Description
 <Describe what the feature or bug that need to be resolved>
 <Description of the big component that encompasses the issue working on>
 <Depencies, ex. libraries, sensors, hardware, small parts of code youhave to work on>
 <ow to do the things>
 NOTE: if you import anything new add it to the list in `requirements.txt`

Follow the sequence diagram in the readme. Make sure to break the logic up into the states as shown in the readme.

1. Setup Phase
- Waiting for input from screw switch (powered off - no code needed)
2. Standby Phase
- Initialize sensors, load suboribit csv, sort csv(will be done in suborbit).
- Then in a loop call read necessary data for
3. Powered Flight Phase

4. Coast Phase

5. Recovery

# Acceptance Criteria
 <Write specifically what is need for this issue to be completed>
Code is written has all these phases
- [ ] Setup up phase - waiting for input from screw switch (powered off - no code needed)
- [ ] Standby Phase - initialize sensors, load suboribit csv, sort csv. Then in a
- [ ]

# Dev Notes
[for assignee]<write down your thought process when developing this issue>

# Linked issues
 <If there are any related issues>

<Add to milestone>

PokeyOne, 2022-05-25:
These are the states of main as I understand them:

```mermaid
stateDiagram-v2
  setup   : Setup
  standby : Standby
  abort   : Abort
  power   : Powered Flight
  coast   : Coast
  reco    : Falling + Recovery
  [*] --> setup     : Turn key
  setup --> standby : All setup tasks are complete
  standby --> abort : System manually turned off
  standby --> power : Ignition detection
  power --> coast   : Burnout detection
  coast --> reco    : Apogee detection
  reco --> [*]      : Manual power off
```

**Note**: Falling and recovery are the same state because at that point it doesn't really matter to flight computer. The flaps should be retracted in both.

PokeyOne, 2022-05-25:
Also @klemie, was just thinking, maybe this issue could be narrowed down to just setting up the main to have a state machine, and then the actual states can be broken up into separate issues. Once things are setup to have states, they can be fairly isolated from each other. This way we can have multiple people working at the same time.

this is a bit of a rough idea that I had:

```mermaid
gantt
  title Main State Machine
  dateFormat YYYY-MM-DD
  excludes weekends
  section Milestones

  Assembly Rehearsal           :milestone, assembly, 2022-06-04, 0d
  Second Assembly Rehearsal    :milestone, aseembly2, 2022-06-11, 0d
  System Acceptance Review     :milestone, acceptance, 2022-06-25, 0d

  section Setup

  Setup state machine logic    :active, init, 2022-05-25, 7d

  section Dependencies

  Ignition detection           :        ignition, 2022-05-25, 7d
  Accel and vel calculations   :        accelvel, 2022-05-25, 7d
  Motor burnout detection      :        burnout, after accelvel, 5d
  Apogee detection             :        apogee, after burnout, 5d

  section States

  Setup                        :        setup, 2022-06-01, 2d
  Standby                      :        standby, after init, 4d
  Powered flight               :        powered, after init, 4d
  Coast flight                 :        coasting, after init, 7d
  Recovery                     :        falling, after standby, 2d
```

Got kinda excited about Gantt charts after the ECE 299 lecture today. Some of the tasks will probably need to be adjusted; this was just an idea that I had and ran with it.

Also these charts are just Mermaid JS charts written as text in the GitHub comment, but I could put these somewhere more permanent at some point.

PokeyOne, 2022-05-26:
I put this into in-progress because PR #99 does at least some of this.

Closed 2022-06-09.

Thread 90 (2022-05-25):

Test USB Type-C to ethernet from fridge (?) with Raspberry Pi

TechGal, 2022-05-25:
# Description
 <Describe what the feature or bug that need to be resolved>
 <Description of the big component that encompasses the issue working on>
 <Depencies, ex. libraries, sensors, hardware, small parts of code youhave to work on>
 <ow to do the things>
 NOTE: if you import anything new add it to the list in `requirements.txt`

Choose a sensor indicator and have a diagram for start up sequence that will trigger the indicator

# Acceptance Criteria
 <Write specifically what is need for this issue to be completed>

- [ ] Retrieve connector from fridge in RR
- [ ] Plug in connector and RPi Zero W
- [ ] See if RPi Zero W can be accessed from laptop
- [ ] Relay instructions to Avionics on how to use

# Dev Notes
[for assignee]<write down your thought process when developing this issue>

# Linked issues
 <If there are any related issues>

<Add to milestone>

Closed 2022-06-15.

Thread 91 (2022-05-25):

Put all hardware deadline updates into OpenProject

TechGal, 2022-05-25:
# Description
 <Describe what the feature or bug that need to be resolved>
 <Description of the big component that encompasses the issue working on>
 <Depencies, ex. libraries, sensors, hardware, small parts of code youhave to work on>
 <ow to do the things>
 NOTE: if you import anything new add it to the list in `requirements.txt`

Choose a sensor indicator and have a diagram for start up sequence that will trigger the indicator

# Acceptance Criteria
 <Write specifically what is need for this issue to be completed>

- [ ] Add command module deadlines
- [ ] Add camera mount deadlines
- [ ] Add wiring deadlines
- [ ] Add ground station deadlines

# Dev Notes
[for assignee]<write down your thought process when developing this issue>

# Linked issues
 <If there are any related issues>

<Add to milestone>

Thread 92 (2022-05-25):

Mount electronics on command module

TechGal, 2022-05-25:
# Description
 <Describe what the feature or bug that need to be resolved>
 <Description of the big component that encompasses the issue working on>
 <Depencies, ex. libraries, sensors, hardware, small parts of code youhave to work on>
 <ow to do the things>
 NOTE: if you import anything new add it to the list in `requirements.txt`

Choose a sensor indicator and have a diagram for start up sequence that will trigger the indicator

# Acceptance Criteria
 <Write specifically what is need for this issue to be completed>

- [ ] Review needed wiring channels with Scott
- [ ] Get CM printed
- [ ] Mount electronics to outside of CM
- [ ] Assemble batteries in CM

# Dev Notes
[for assignee]<write down your thought process when developing this issue>

# Linked issues
 <If there are any related issues>

<Add to milestone>

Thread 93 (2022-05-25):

Spec ground station equipment

TechGal, 2022-05-25:
# Description
 <Describe what the feature or bug that need to be resolved>
 <Description of the big component that encompasses the issue working on>
 <Depencies, ex. libraries, sensors, hardware, small parts of code youhave to work on>
 <ow to do the things>
 NOTE: if you import anything new add it to the list in `requirements.txt`

Choose a sensor indicator and have a diagram for start up sequence that will trigger the indicator

# Acceptance Criteria
 <Write specifically what is need for this issue to be completed>

- [x] Spec LNA, limiter, crossed-yagi antenna for groundstation
- [x] Send list to Levente for feedback
- [x] On response, add to procurement sheet

# Dev Notes
[for assignee]<write down your thought process when developing this issue>

# Linked issues
 <If there are any related issues>

<Add to milestone>

Closed 2022-06-15.

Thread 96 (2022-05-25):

Write testing plans

TechGal, 2022-05-25:
# Description
 <Describe what the feature or bug that need to be resolved>
 <Description of the big component that encompasses the issue working on>
 <Depencies, ex. libraries, sensors, hardware, small parts of code youhave to work on>
 <ow to do the things>
 NOTE: if you import anything new add it to the list in `requirements.txt`

Choose a sensor indicator and have a diagram for start up sequence that will trigger the indicator

# Acceptance Criteria
 <Write specifically what is need for this issue to be completed>

- [ ] Low Power Test
- [ ] Battery Drain Test
- [ ] Avionics / Recovery Integration Test
- [ ] Other tests in the folder

# Dev Notes
[for assignee]<write down your thought process when developing this issue>

# Linked issues
 <If there are any related issues>

<Add to milestone>

macsyd, 2022-06-30:
@TechGal status update? -Kris

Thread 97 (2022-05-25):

How to use ground station as full duplex receiver

TechGal, 2022-05-25:
# Description
 <Describe what the feature or bug that need to be resolved>
 <Description of the big component that encompasses the issue working on>
 <Depencies, ex. libraries, sensors, hardware, small parts of code youhave to work on>
 <ow to do the things>
 NOTE: if you import anything new add it to the list in `requirements.txt`

Choose a sensor indicator and have a diagram for start up sequence that will trigger the indicator

Note that each transmitter will be sending at 1Hz.

# Acceptance Criteria
 <Write specifically what is need for this issue to be completed>

- [ ] How to set up an RTL-SDR to receive two signals at once (full duplex), or monitor two frequencies at once (half duplex)
- [ ] Update software on ground station to include this
- [ ] Test receiving two signals at once

# Dev Notes
[for assignee]<write down your thought process when developing this issue>

# Linked issues
 <If there are any related issues>

<Add to milestone>

Closed 2022-06-30.

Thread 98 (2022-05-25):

Find out if antenna for TeleGPS needs to be bigger

TechGal, 2022-05-25:
# Description
 <Describe what the feature or bug that need to be resolved>
 <Description of the big component that encompasses the issue working on>
 <Depencies, ex. libraries, sensors, hardware, small parts of code youhave to work on>
 <ow to do the things>
 NOTE: if you import anything new add it to the list in `requirements.txt`

Choose a sensor indicator and have a diagram for start up sequence that will trigger the indicator

# Acceptance Criteria
 <Write specifically what is need for this issue to be completed>

- [ ] Find out what ground station setup is using
- [ ] Use Link-Budget spreadsheet to calculate margin for TeleGPS
- [ ] Look into antennas for TeleGPS is needed
- [ ] Talk to Ryan about space in MAGPI for an antenna

# Dev Notes
[for assignee]<write down your thought process when developing this issue>

# Linked issues
 <If there are any related issues>

<Add to milestone>

Closed 2022-06-30.

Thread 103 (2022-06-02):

X1-AV-46 Main: Standy Function

JackCotter, 2022-06-02:
# Description
 The main function is in the standby function until it is launched. Check ONE appropriate sensor in a loop for a large difference in the rockets position indicating launch. Once launch is detected return from the function.
 NOTE: if you import anything new add it to the list in `requirements.txt`

# Acceptance Criteria
 <Write specifically what is need for this issue to be completed>
- [ ]    AC 1

# Dev Notes
[for assignee]<write down your thought process when developing this issue>

# Linked issues
 <If there are any related issues>

<Add to milestone>

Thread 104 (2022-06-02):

X1-AV-47 poweredFlight Function

JackCotter, 2022-06-02:
# Description
This function is used when motor is at full power. Read Sensors, send data to ground station, send data to calculations but do not deploy air brakes. Return from Function when motor is no longer at full power. Detect when motors are no longer at full power or 5 seconds has elapsed.
 NOTE: if you import anything new add it to the list in `requirements.txt`

# Acceptance Criteria
 <Write specifically what is need for this issue to be completed>
- [ ]    AC 1

# Dev Notes
[for assignee]<write down your thought process when developing this issue>

# Linked issues
 <If there are any related issues>

<Add to milestone>

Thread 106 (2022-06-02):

X1-AV-48 coast_flight Function

JackCotter, 2022-06-02:
# Description
 This function is used when rocket is coasting. Read Sensors, send data to ground station, send data to calculations and deploy air brakes as appropriate. Return from Function when rocket hits apogee. Detect when apogee is achieved.
 NOTE: if you import anything new add it to the list in `requirements.txt`

# Acceptance Criteria
 <Write specifically what is need for this issue to be completed>
- [ ]    AC 1

# Dev Notes
[for assignee]<write down your thought process when developing this issue>

# Linked issues
 <If there are any related issues>

<Add to milestone>

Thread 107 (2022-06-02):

X1-AV-49 recovery Function

JackCotter, 2022-06-02:
# Description
 This function is used when rocket is falling (after apogee/y velocity at zero). Read Sensors, send data to ground station, send data to calculations but do not deploy air brakes. Return from Function when rocket stops moving.
 NOTE: if you import anything new add it to the list in `requirements.txt`

# Acceptance Criteria
 <Write specifically what is need for this issue to be completed>
- [ ]    AC 1

# Dev Notes
[for assignee]<write down your thought process when developing this issue>

# Linked issues
 <If there are any related issues>

<Add to milestone>

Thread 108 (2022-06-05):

Update All Files to Use `snake_case` for Variables and Methods.

PokeyOne, 2022-06-05:
# Description

There are many places where we will used `snake_case` in one file and then in another file we will use `lowerCamelCase` and `UpperCamelCase`. We should be just using `snake_case` for all functions and variables. This does not apply to classes.

One example of this is in the `gpioReader.py` file. This should be `gpio_reader.py` and inside all methods should be transformed to snake case as well.

# Acceptance Criteria

- [ ] All variables are snake case
- [ ] All functions are snake case
- [ ] All file names are snake case

# Dev Notes

[for assignee]<write down your thought process when developing this issue>

krislemie, 2022-07-15:
can you pull in the changes from refactor and update accordingly?

PokeyOne, 2022-07-15:
@krislemie Yes, but after assembly rehearsal I think is a better time. This is just a style thing and isn't strictly necessary right now. After assembly rehearsal I'll update the PR and then we can merge it.

Closed 2022-11-17.

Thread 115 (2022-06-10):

Ground Timeout Detection

PokeyOne, 2022-06-10:
# Description

Once the rocket is on the ground we should have a way for the Pi to stop logging information and cleanup active things. This is because the FC will be constantly writing data to BB, and if we were to just shut off FC, it may leave currupted data. Having FC stop logging after a certain amount of time would be ideal.

## How to Detect

There are two main modes of detection that were discussed:
1. General timeout (for example, expected flight time + 10 minutes)
2. Detection of ground (plus a five minute buffer or something)

# Acceptance Criteria

- [ ] Assess whether data curuption would even be a real issue.
- [ ] Assess and decide on the approppriate way to detect this.
- [ ] Implement detection
- [ ] Stop logging data some time after detection.
- [ ] There should be a buffer between detection and stopping logging.
- [ ] There should be a minimum time before it even considers stopping logging.
- [ ] It should **only be able to stop loggin in the recovery state**. It would be very bad if we just stopped logging in the middle of the burn.

PokeyOne, 2022-06-10:
Also something I just thought about:

This might not be super important.

As far as I am aware there are only two types of data being stored:
1. Text (for the csv)
2. Images from cameras

The text can never really be currupted because it should just be appending, and the worst case is an unfinished row in the csv that we can manually edit.

For the images, if we are just storing images every certain period, we may just end up with one unfinished frame. This should leave the rest of the frames just fine.

So have this task might just be making things needlessly complicated.

PokeyOne, 2022-06-10:
Following some discussion in the Discord:

This is probably still worth it in some form.

Another way we could do this is through detecting when the transmitter stops responding and then stop. This way we could just shut down the transmitter and then wait five seconds before turning off the pi.

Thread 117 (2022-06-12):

X1-AV-61 Update GPIO pins in sensor classses

klemie, 2022-06-12:
# Description
 <Describe what the feature or bug that need to be resolved>
 <Description of the big component that encompasses the issue working on>
 <Depencies, ex. libraries, sensors, hardware, small parts of code youhave to work on>
 <ow to do the things>

We need to set up all the pins that sensors are connected to in their sensor classes. Go to the wiring diagram on Alex's branch and follow the labels to the pi. Use CONSTANTS for the pins at the top of the files.

# Acceptance Criteria
 <Write specifically what is need for this issue to be completed>

- [ ] bme.py, lsm.py, adx.py, hx711s.py are updated with GPIO pins initialized
- [ ] GPIO is sourced from Alexs wiring diagram

# Dev Notes
[for assignee]<write down your thought process when developing this issue>

# Linked issues
 <If there are any related issues>

<Add to milestone>

krislemie, 2022-06-29:
Sensors do this automatically. Might have to fix something with bus addressing

Closed 2022-06-30.

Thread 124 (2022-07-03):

Remove tare() function from HX711-Multi.py

jjderooy, 2022-07-03:
# Description
Realized the tare() function is necessary since we can tare based on the on the rail strain values after the flight is over. This removes our numpy dependency (at least from this file).

# Acceptance Criteria
- [ ]    Delete the tare() function and fix any of it's integrations into the other functions.

# Dev Notes
[for assignee]<write down your thought process when developing this issue>

# Linked issues
 <If there are any related issues>

<Add to milestone>

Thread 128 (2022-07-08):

X1-AV-64 Refactor Sensor Classes to Simply

JackCotter, 2022-07-08:
# Description

hrmm

# Acceptance Criteria
 <Write specifically what is need for this issue to be completed>
- [ ]    AC 1

# Dev Notes
[for assignee]<write down your thought process when developing this issue>

# Linked issues
 <If there are any related issues>

<Add to milestone>

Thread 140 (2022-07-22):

X1-AV-67 Write camera.py

JackCotter, 2022-07-22:
# Description
 <Describe what the feature or bug that need to be resolved>
 <Description of the big component that encompasses the issue working on>
 <Depencies, ex. libraries, sensors, hardware, small parts of code youhave to work on>
 <ow to do the things>
 NOTE: if you import anything new add it to the list in `requirements.txt`

# Acceptance Criteria
 <Write specifically what is need for this issue to be completed>
- [ ]    AC 1

# Dev Notes
[for assignee]<write down your thought process when developing this issue>

# Linked issues
 <If there are any related issues>

<Add to milestone>

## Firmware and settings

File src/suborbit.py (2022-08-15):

import csv
import numpy
import functools
from collections import namedtuple

# Rocket mass in kg, including the fuel grain
ROCKET_WET_MASS = 20.493
FUEL_GRAIN_MASS = 3.423
ROCKET_DRY_MASS = ROCKET_WET_MASS - FUEL_GRAIN_MASS

# TODO: Is this needed anywhere
ROCKET_AREA = 0.011050733

# Data type for storing elements of rocket position
#
# Seems roughly equivalent a struct in other compiled languages (i.e. C, Rust)
RocketPosition = namedtuple("RocketPosition", [
    "altitude", "velocity", "acceleration"
])

# TODO: !MC - Possibly rename this because there is a class in the Xenia stuff
#       that has the same name. Maybe call this FlightData??
class DragData:
    """Storage of rocket information to be used for predictions.

    Fields
    ------
    cd_no_airbrakes_data:
      Drag coefficient with no airbrakes. Each element of the array is an array
      of mach number, cd area with power on, and cd area with no power.
    """

    def __init__(self, cd_no_airbrakes_path):
        """Initialize a new DragData object with the data specified.

        Panics
        ------
        The method will exit with status code 1 if any of the files could
        not be opened succesfully.

        Params
        ------
        cd_no_airbrakes_path:
            The path relative to program execution to the csv data for the
            coefficient of drag without airbrakes.
        """

        self.cd_no_airbrakes_data = []

        try:
            # Open the file.
            cd_no_airbrakes_file = open(cd_no_airbrakes_path, newline = '')

            cd_no_airbrakes_csv_reader = csv.reader(cd_no_airbrakes_file)
            # Store the data.
            for (i, row) in enumerate(cd_no_airbrakes_csv_reader):
                if i == 0:
                    continue
                self.cd_no_airbrakes_data.append(numpy.array(row).astype(float))

            # Close the files.
            cd_no_airbrakes_file.close()
        except:
            print("Couldn't open file")
            exit(1)

        self.cd_no_airbrakes_data.sort(key=functools.cmp_to_key(compare_drag_row))


def compare_drag_row(a, b):
    return a[0] - b[0]


def flap_area_from_degrees(degrees):
    """Get the flap area in meters squared from the degrees of opening.

    Degrees is the angle from closed in degrees, and area is in meters squared.
    """
    return -4.0e-7 * (degrees**2) + 9e-5 * degrees + 5e-5


def find_drag_coefficient(data, mach_number):
    """Binary search drag coefficient data.

    This could be accomplished with the bisect.bisect_left method in
    Python 3.10, but the Pi can only run 3.7 unless we complile from source.

    Params
    ------
    data:
      This should either be the cd_no_airbrakes_data array in a DragData object.

    mach_number:
      The desired mach number to look for.
    """
    if len(data) == 0:
        return [mach_number, 0.0, 0.0]

    if len(data) == 1:
        return data[0]

    index = int(len(data)/2)
    start = 0
    end = len(data)

    while end - start > 2:
        if data[index][0] < mach_number:
            start = index
        else:
            end = index

        index = int((end - start) / 2) + start

    return data[start]


def atmosphere(altitude):
    """Calculate the speed of sound and air density at a given altitude.

    This function is taken from atmosisa and atmoslapse functions in matlab,
    which are based on the International Standard Atmospher Model. This also
    simplifies the calculations by using standard atmospheric values. These
    values were also used in the Matlab Library.

    Params
    ------
    altitude:
      The altitude in meters.

    Returns
    -------
    The return value is a tuple[float, float]
    Where the first float is the speed of sound in meters per second,
    and the second float is the air density in kilograms per meter cubed.
    """
    # Scalar acceleration due to gravity in metere per second squared.
    gravity = 9.80665
    # Scalar specific heat ratio
    specific_heat_ratio = 1.4
    # Scalar characteristic gas constant joules per kilogram-kelvin.
    characteristic_gas_constant = 287.0531
    # Scalar lapse rate in kelvin per meter.
    lapse_rate = 0.0065
    # Height of troposphere in meters.
    troposphere_height = 11000
    # Height of tropopause in meters.
    tropopause_height = 20000
    # Air density at mean sea level in kilograms per meter cubed.
    air_density_at_sea_level = 1.225
    # Static pressure at mean sea level in pascal.
    static_pressure_at_sea_level = 101325
    # TODO: !MC - We may need this to be variable for launch day??
    # Scalar absolute temperature at mean sea level in kelvin.
    absolute_temperature_at_sea_level = 288.15

    # TODO: !MC - Replace these in the equations with the full names. These just
    #       happen to be what the matlab script used.
    h = altitude
    g = gravity
    gamma = specific_heat_ratio
    r = characteristic_gas_constant
    l = lapse_rate
    hts = troposphere_height
    htp = tropopause_height
    rho0 = air_density_at_sea_level
    p0 = static_pressure_at_sea_level
    t0 = absolute_temperature_at_sea_level
    h0 = 0

    if h > htp:
        h = htp

    if h < h0:
        h = h0

    # TODO: min function??
    h_tmp = h
    if h > hts:
        h_tmp = hts

    t = t0 - l * h_tmp

    expon = 1
    if h > hts:
        expon = numpy.exp((g / (r * t)) * (hts - h))

    a = numpy.sqrt(t * gamma * r)

    theta = t / t0

    rho = rho0 * pow(theta, (g / (l*r)) - 1.0) * expon

    return (a, rho)


def grav(alt):
    """Calculate gravity at a certain altitude in meters.

    Params
    ------
    alt:
      Altitude in meters.
    """
    # This gravity was just set based on an only estimator for
    # Cochrane Ontario, using a base elevation of 275m for ground level,
    # adding 5000ft for the middle of flight ish. The idea was that this
    # would be faster, but the benefits are negligable.
    return 9.805#(6.67408e-11 * 5.972e24) / pow((6.371e6 + alt), 2)


class Suborbit:
    def __init__(self):
        self.data = DragData("/home/pi/Xenia1-flight-Computer/drag_data/cda_no_airbrakes.csv")
        self.previous_sim = None


    def calc_airbrakes_position(self, current_alt, estimated_alt, current_brakes):
        apogee_alt_diff = estimated_alt - 3048
        current_alt_diff = current_alt - 3048

        movement = 10.0
        if abs(apogee_alt_diff < 1000):
            movement *= 0.5
        
        if abs(apogee_alt_diff < 500):
            movement *= 0.5

        if abs(apogee_alt_diff < 100):
            movement *= 0.5

        movement *= apogee_alt_diff / abs(apogee_alt_diff)

        result = current_brakes + movement

        if result < 0:
            return 0.0
        elif result > 100:
            return 100.0

    def run(self, alt, vel, accel, airbrakes, dry_mass = ROCKET_DRY_MASS):
        """
        Calculate the height of apogee and how long until apogee.

        Params
        ------
        alt:
            Altitude in meters
        vel:
            Velocity in meters per second
        accel:
            Acceleration in meters per second per second
        airbrakes:
            The amount of airbrakes currently deployed. For example, 0.8 would
            mean that airbrakes are 80% deployed.


        Returns
        -------
        The value returned with be of type (float, float), containing the max
        altitude in meters, and the time until the rocket gets there.
        """
        if not ((not alt is None) and (not vel is None) and (not accel is None)):
            if self.previous_sim:
                return self.previous_sim
            else:
                return self.run(0, 0, 0, 0.0)

        initial_position = RocketPosition(alt, vel, accel)

        # Intentionally ignoring any sort of power phase because not needed.

        # This will return (float, float)
        res = self.__coast(initial_position, dry_mass, airbrakes, 0.0, self.data)

        self.previous_sim = res

        return res

    def __coast(
            self,
            initial_position,
            mass,
            airbrakes_amount,
            time,
            data
    ):
        """Rocket coasting to apogee after motor shut down.

        Params
        ------
        initial_position:
            The position of the rocket at the start of the coast phase.
        mass:
            The mass of the rocket during the coast phase.
        airbrakes_amount:
            The ratio of airbrakes to no airbrakes as a decimal. For example,
            0.8 would mean airbrakes 80% out.
        data:
            The data object that contains the drag coefficient LUT.
        """
        # TODO: !MC - Remove the data parameter and use self.data

        # Fixed dt because we are only ever using one data set.
        time_delta = 0.1
        last_position = initial_position

        while last_position.velocity > 0:

            # TODO: Use better variables than a and rho
            #       speed_of_sound and air_density
            # Calculate atmospheric conditions
            (a, rho) = atmosphere(last_position.altitude)

            # Calculate drag force.
            m_temp = last_position.velocity / a
            # TODO: !MC - When running the actual rocket, this will have to do some
            #       mixing between the airbrakes and no_airbrakes data based on the
            #       current_airbrakes position.

            # Index of one is the power off CdA
            cda_no_airbrake = find_drag_coefficient(
                data.cd_no_airbrakes_data,
                m_temp
            )[1]

            # TODO: 1.1 is constant for flap Cd, 80.0 should be the max angle of airbrakes.
            #       These should be global constants, and the max angle should be adjusted.
            # TODO: Actually just change the airbrakes_amount to airbrakes_degrees. Easier that way. And I think easier for FC to compute.
            drag_area_coefficient = cda_no_airbrake + 1.1 * flap_area_from_degrees(airbrakes_amount * 80.0)
            drag = drag_area_coefficient * 0.5 * rho * pow(last_position.velocity, 2)

            g = grav(last_position.altitude)

            accel = -drag / mass - g
            vel = last_position.acceleration * time_delta + last_position.velocity
            alt = last_position.velocity * time_delta + ((last_position.acceleration * pow(time_delta, 2)) / 2) + last_position.altitude

            # Check if we have hit the ground (Hopefully not!)
            if alt < initial_position.altitude:
                accel = 0
                vel = 0
                alt = initial_position.altitude

            last_position = RocketPosition(alt, vel, accel)

            # I'm not sure why it is going for plus one and plus two, but that was
            # what the original script did.
            time += time_delta

        return (last_position.altitude, time)


################################################################################
# Tests
#
# TODO: Move tests to own file
################################################################################

def test_data_loading():
    data = DragData("drag_data/cda_no_airbrakes.csv")

def test_running():
    so = Suborbit()

    (max_alt, max_time) = so.run(552.7, 352.45, -9.8, 0.0)
    (min_alt, min_time) = so.run(552.7, 352.45, -9.8, 1.0)
    print("max: alt =", max_alt, "time =", max_time)
    print("min: alt =", min_alt, "time =", min_time)

def run_tests():
    test_data_loading()
    test_running()
    print("All tests passed!")

if __name__ == "__main__":
    run_tests()

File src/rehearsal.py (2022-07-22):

# Rehearsal script
#
# This script is meant to be run during the assembly rehearsal instead of main
# that will do the things with the sensors.
#
# MOST LOGIC SHOULD BE IN THE MAIN CODE. In theory, this should be only calling
# functions and controlling the flow.

import board
import math
import csv
import time
from airbrakes import Airbrakes
from adafruit_bme280 import basic as adafruit_bme280
import adafruit_lsm9ds1
import adafruit_adxl34x
import RPi.GPIO as GPIO
import busio
from sensors.bme import Bme
from sensors.lsm import Lsm
from sensors.adx import Adx
from sensors.hx711s import Hx711
from flight_computer import FlightComputer as FC

i2c = board.I2C()

local_time = time.localtime()

lsm = None
adx = None
bme = None
flight_computer = None

def startup():
    """Initialize all the things"""
    global flight_computer
    flight_computer = FC()
    config_sensors()


def init_airbrakes():
    """This should initialize the airbrakes stepper motor and open and close airbrakes

    The main driver for the airbrakes should automatically do this upon
    initialization.

    Don't stand next to the airbrakes at this point.
    """
    airbrakes = Airbrakes(False, 8, 4, 7)
    # This will wave at the fans (move the brakes in and out)
    airbrakes.calibrate()
    airbrakes.deployBrakes(0)


def read_hx711s():
    """Basically like zeroing a scale, but with the strain gauges"""
    if strain_gauges.isReady():
        strain_gauges.readRaw()

def config_sensors():
    """Test readings from sensors, returns true if all sensors read something"""
    global bme
    global i2c
    global lsm
    global adx
    global strain_gauges

    lsm = Lsm(i2c)
    adx = Adx(i2c)
    bme = Bme(i2c)
    strain_gauges = Hx711()

    lsm.refresh()
    adx.refresh()
    bme.refresh()

    print("bme Temperature:", bme.temperature)
    print("Lsm Temperatrue:", lsm.temperature)
    print("Lsm Acceleration:", lsm.acceleration)
    print("Adx Acceleration:",  adx.acceleration)


def gather_data():
    """
    Collect data once and return. Data in blackbox will show up as a csv

    Order of collected data:
        Timestamp
        [bme]: temperature, humidity, pressure, altitude
        [lsm]: acceleration: x, y, z; magnometer: x, y, z; gyroscope: x, y, z, temperature
        [adx]: acceleration: x, y, z
    """
    global lsm
    global bme
    global adx

    lsm.refresh()
    bme.refresh()
    adx.refresh()

    lsm_acc_x, lsm_acc_y, lsm_acc_z = lsm.acceleration
    lsm_mag_x, lsm_mag_y, lsm_mag_z = lsm.magnetic
    lsm_gyro_x, lsm_gyro_y, lsm_gyro_z = lsm.gyro
    lsm_temp = lsm.temperature

    bme_temp = bme.temperature
    bme_alt = bme.altitude
    bme_hum = bme.humidity
    bme_press = bme.pressure

    adx_acc_x, adx_acc_y, adx_acc_z = adx.acceleration
    timestamp = time.strftime("%H:%M,%S", local_time)

    return [
        timestamp,
        bme_temp,
        bme_hum,
        bme_press,
        bme_alt,
        lsm_acc_x,
        lsm_acc_y,
        lsm_acc_z,
        lsm_mag_x,
        lsm_mag_y,
        lsm_mag_z,
        lsm_gyro_x,
        lsm_gyro_y,
        lsm_gyro_z,
        lsm_temp,
        adx_acc_x,
        adx_acc_y,
        adx_acc_z
    ]

def send_to_black_box(data, f):
    writer = csv.writer(f)
    writer.writerow(data)


def rehearsal():
    global flight_computer
    startup()
    # one minute of reading
    time_out = time.time() + 60
    f = open('/media/pi/XENIA-1_BB/rehearsal.txt', 'a')
    send_to_black_box("Here is the order of values: \n timestamp, bme_temp, bme_hum, bme_press, bme_alt, lsm_acc_x, lsm_acc_y, lsm_acc_z, lsm_mag_x, lsm_mag_y, lsm_mag_z, lsm_gyro_x, lsm_gyro_y, lsm_gyro_z, lsm_temp, adx_acc_x, adx_acc_y, adx_acc_z \n\n", f)
    while True:
        if time.time() > time_out:
            break
        data = gather_data()
        send_to_black_box(data, f)

    f.close()

    flight_computer.beep()
    flight_computer.beep()

if __name__ == "__main__":
    rehearsal()

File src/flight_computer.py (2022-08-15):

import board

import time
from airbrakes import Airbrakes
import RPi.GPIO as GPIO
import busio
from rocketData import RocketData
import numpy as np
import suborbit

from HX711Multi import HX711_Multi

# Gees required to exit standby. This G load must be sustained for a certain time
# TODO CHECK THESE WITH CLAIRE AND FIGURE OUT IF THEY ARE IN G or m/s
STANDBY_ACCELERATION_THRESHOLD = 3*9.81
POWERED_FLIGHT_EXIT_THRESHOLD = -9

# Motor burn time is 3s according to data sheet.
POWERED_TIMEOUT = 3*1.15

#  From flight dynamics.
COAST_TIMEOUT = 300

# Under parachute from max apogee of 14000ft, the rocket takes 310s to descend.
RECOVERY_TIMEOUT = 310*1.5
BUZZ_PIN = 21

# BLACKBOX_FILEPATH = "/media/pi/black_box"
BLACKBOX_FILEPATH = "/media/black_box/flight_data_" + str(time.strftime("%H-%M-%S")) + ".txt"

def mach(n):
    return 339.0 * n

class FlightComputer:
    def __init__(self):
        print("initting the FC")
        self.rocket_data = RocketData()

        print("Attempting to open file")
        self.black_box = open(BLACKBOX_FILEPATH , "a+")


        print("Suborbit")
        self.suborbit = suborbit.Suborbit()

        print("Airbrakes")
        self.airbrakes = Airbrakes(False, 8, 4, 7)

        print("Startup")
        self.startup()
        print("Seatbelt sign is on (FC is initialized)")


    def startup(self):
        """Initialize all the things"""

        print("Sensor roll call\n  buzzer")
        self.__config_buzzer()
        self.beep(duration = 1) 
        time.sleep(5)

        if self.rocket_data.lsm_sensor_ready():
            # lsm sensors read correctly
            print("  lsm init successfully")
        else:
            self.beep(count = 1)
            time.sleep(3.0)
            print("  lsm failed to init")

        if self.rocket_data.bme_sensor_ready():
            # bme sensors read correctly
            print("  bme init successfully")
        else:
            self.beep(count = 2)
            time.sleep(3.0)
            print("  bme failed to init")

        if self.rocket_data.adx_sensor_ready():
            # adx sensors read correctly
            print("  adx init successfully")
        else:
            self.beep(count = 3)
            time.sleep(3.0)
            print("  adx failed to init")

        if self.airbrakes.calibrate():
            print("  airbrakes init successfully")
        else:
            self.beep(count = 4)
            time.sleep(3.0)
            print("  airbrakes failed to init")
        self.airbrakes.deployBrakes(0)
        self.beep(duration = 1) 
        time.sleep(5)

    def __config_buzzer(self):
        GPIO.setup(BUZZ_PIN, GPIO.OUT)


    def beep(self, duration = 0.2, count = 1):
        """
        This method should buzz the buzzer. Different durations mean different
        things, default of 0.2 indicate success
        """
        print("beeping", count, "times, for", duration, "seconds")
        
        return 

        for i in range(count):
            if not i is 0:
                time.sleep(duration)
            

            GPIO.output(BUZZ_PIN, GPIO.HIGH)
            time.sleep(duration)
            GPIO.output(BUZZ_PIN, GPIO.LOW)


    def vec_len(v):
        return np.sqrt(np.dot(v, v))


    def __standby(self):
        self.airbrakes.sleep()
        while True:
            print("Stnadby")
            self.rocket_data.refresh()
            self.rocket_data.send_to_black_box(self.black_box)
            current_accel = FlightComputer.vec_len(self.rocket_data.current_acceleration)
            if current_accel < STANDBY_ACCELERATION_THRESHOLD:
                timer = time.time()
                if abs(timer - time.time()) > 1:
                    break


    def __powered_flight(self):
        time_at_start = time.time()

        while True:
            print("Powered Flight")
            self.rocket_data.refresh()
            self.rocket_data.send_to_black_box(self.black_box)
            if time.time() > (time_at_start + POWERED_TIMEOUT) or self.rocket_data.current_acceleration < POWERED_FLIGHT_EXIT_THRESHOLD:
                break


    def __coast_flight(self):
        time_at_start = time.time()
        self.airbrakes.wake()
        subo = suborbit.Suborbit()


        AIRBRAKES_HOLD_TIMEOUT = 4.0

        ts = time.time()
        airbrakes_released = False

        while True:
            print("Coast flight")
            self.rocket_data.refresh()
            self.rocket_data.send_to_black_box(self.black_box)

            if not (time.time() - ts >= AIRBRAKES_HOLD_TIMEOUT or airbrakes_released):
                if (not self.rocket_data.velocity is None) and self.rocket_data.velocity < mach(0.75):
                    airbrakes_released = True
                    print("airbrakes set free because of velocity")
                continue

            if not airbrakes_released:
                airbrakes_released = True
                print("airbrakes set free because of timeout")

            self.rocket_data.airbrakes_percentage = self.airbrakes.get_position()

            alt = self.rocket_data.current_altitude
            vel = self.rocket_data.velocity
            accel = self.rocket_data.current_acceleration
            self.rocket_data.update_airbrakes_percentage(self.airbrakes.get_position())
            airbrakes = self.rocket_data.airbrakes_percentage

            (max_alt, max_time) = self.suborbit.run(alt, vel, accel, airbrakes)
            new_airbrakes_position = subo.calc_airbrakes_position(alt, max_alt, airbrakes)
            self.airbrakes.deployBrakes(new_airbrakes_position)

            if time.time() > (time_at_start + COAST_TIMEOUT) or (self.rocket_data.velocity and self.rocket_data.velocity < 0):
                break


    def __recovery_flight(self):
        time_at_start = time.time()

        while True:
            print("Recovery Flight")
            self.rocket_data.refresh()
            self.rocket_data.send_to_black_box(self.black_box)
            if time.time() > (time_at_start + RECOVERY_TIMEOUT):
                break
            elif self.rocket_data.velocity == 0:
                break


    def fly(self):
        self.__standby()
        self.__powered_flight()
        self.__coast_flight()
        self.__recovery_flight()
        self.black_box.close()

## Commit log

2021-09-09 Reworked GPIO Reader class to read bme280 sensor. Functionality has been added to setup sensor for I2C connection and is ready for phyical testing on board. To use: create gpioReader object, then cal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
2022-03-03 Tidy code, syntactic errors
    [airbrakes.py]
2022-03-14 Fix rest of revisons.
    [airbrakes.py]
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2022-03-18 Schematic back to october version
    Back to where I was in october, with two sensors
    [Xenia-1-rocket-schematic.sch.kicad_sch]
2022-03-18 Fix step delay logic. Revisons
    [airbrakes.py]
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2022-03-24 Changing the power pins to wires
    All the ground pins have been connected to the ground pin 9, and all the power pins are now connected to wires.
    [Xenia-1-rocket-schematic.sch.kicad_sch]
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2022-03-31 Added more components
    Analog to digital converter added.
    Black box added and pushed to diagram.
    [Xenia-1-rocket-schematic.sch.kicad_sch]
2022-04-01 Removed first version
    First version was in Kicad 5, second version is in kicad 6
    [Xenia-1-rocket-schematic.kicad_pcb, Xenia-1-rocket-schematic.sch]
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2022-04-02 Made new components
    Made a symbol called pi ports to connect ground and 9 volt as well as the camera port.
    [Xenia-1-rocket-schematic.sch.kicad_sch]
2022-04-02 Symbol names updated
    Pi parts have been updated, and many things have been renamed
    [Xenia-1-rocket-schematic.sch.kicad_sch]
2022-04-02 New components
    Added the Analog to Digital converter to the schematic. Also created the stepper motor and added to schematic.
    [Xenia-1-rocket-schematic.sch.kicad_sch]
2022-04-06 Updated the schematic
    The motor controller has been wired, SDA pin on IMU changed, and a stepper motor has been added
    [Xenia-1-rocket-schematic.sch.kicad_sch]
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2022-04-08 Updating schematic
    Connecting pins to the 5V line and adding a GPIO port allocation to the stepper motor controller.
    [Xenia-1-rocket-schematic.sch.kicad_sch]
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2022-04-10 Converted strain guages to list & error checks
    [rocketData.py]
2022-04-12 Schematic updates
    Changed GPIO pins so SCL and SDA are assigned. Also put pins on the Analog to Digital converter.
    [Xenia-1-rocket-schematic.sch.kicad_sch]
2022-04-12 Updated schematic
    Added a voltage to VDD and ground on the analog to digital converter.
    [Xenia-1-rocket-schematic.sch.kicad_sch]
2022-04-12 More schematic updates
    Added a potentiometer and marked some ports not connected.
    [Xenia-1-rocket-schematic.sch.kicad_sch]
2022-04-13 Schematic update
    Made an update to the analog to digital converter symbol.
    [Xenia-1-rocket-schematic.sch.kicad_sch]
2022-04-13 Updated schematic
    Changed the voltage on the analog to digital converter to 5 volts and added voltage and ground to the potentiometer.
    [Xenia-1-rocket-schematic.sch.kicad_sch]
2022-04-20 Updated schematic
    Thanks to advice from Aila, schematic has been updated to make sure that things looking better.
    Will take the other advice into consideration.
    [Xenia-1-rocket-schematic.sch.kicad_sch]
2022-04-20 Schematic updated
    Schematic updated to have the voltages going up and the ground rail connected to ports on the pi.
    [Xenia-1-rocket-schematic.sch.kicad_sch]
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2022-04-20 Updated schematic
    Schematic updated with some of the step, sleep and dir pins on the pin.
    [Xenia-1-rocket-schematic.sch.kicad_sch]
2022-04-20 Updated schematic
    Changed GPIO 18 to Enable and connected Sleep to ground
    [Xenia-1-rocket-schematic.sch.kicad_sch]
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2022-05-15 Revert "Camera Testing Done by Maia"
    This reverts commit 5d49dfd883abf1363ec7f12fb8b1234ad5cbdbe3.
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2022-05-26 Remove uses of failing modules in main.py
    [rocketData.py]
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2022-05-27 Schematic update
    Started work on making the wired version of the schematic, will be extremely messy even with everything subdivided into different sections for sides of the avionics bay
    [Xenia-1-rocket-schematic.sch.kicad_sch]
2022-06-02 Updated schematic
    The wire section has had some work done to it, and I will continue with labeling everything to make sure that the wiring works out
    [Xenia-1-rocket-schematic.sch.kicad_sch]
2022-06-04 Updating schematic
    Changed sensors around and made several more sensors and wired them.
    [Xenia-1-rocket-schematic.sch.kicad_sch]
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2022-06-06 Updated schematic
    Wired the transmitter and moved every sensor to the I2C area and wired them all to SDI and SCL
    [Xenia-1-rocket-schematic.sch.kicad_sch]
2022-06-07 Updated the schematic
    Labeled the sides of the avionics bay and wired the buzzer to the DIR pin
    [Xenia-1-rocket-schematic.sch.kicad_sch]
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2022-06-08 Schematic updated
    Added a several new labels on the wiring diagram and made a section for the recovery altimeters, also made the e-matches necessary to light the black powder. Added recurring labels to wires on the ri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
    [Xenia-1-rocket-schematic.sch.kicad_sch]
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2022-06-11 Updated Schematic
    Added a second sheet, and made a new version of the schematic that is a lot more organized
    [Xenia-1-rocket-schematic.sch.kicad_sch, untitled.kicad_sch]
2022-06-11 Updated Schematic
    Made a couple adjustments to the schematic with the size of things and put a couple labels up
    [Xenia-1-rocket-schematic.sch.kicad_sch, untitled.kicad_sch]
2022-06-12 Updated schematic
    Added some labels to the second version of the wired schematic about what sides of the avionics bay things went to.
    [Xenia-1-rocket-schematic.sch.kicad_sch, untitled.kicad_sch]
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2022-06-16 Updated schematic
    Made the schematic line up with the actual avionics bay
    [Xenia-1-rocket-schematic.sch.kicad_sch]
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2022-06-18 some more schematic touchups and labelling a loose end
    [Xenia-1-rocket-schematic.sch.kicad_sch]
2022-06-18 buzz buzz
    Added step to the rehearsal script that will buzz the buzzer to indicate complete setup
    [rehearsal.py]
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2022-07-07 Removed altitude_temperature_v1
    Axed altitude_temperature_v1 because it makes me very sad to look at. v2 should work fine, and should actually be less error prone, however I have copied v1 into another location in case it needs to be used for some ungodly reason (I really hope we won’t have to though)
2022-07-09 updated lsm, bme, adx according to issue X1-AV-64
    [adx.py, bme.py, lsm.py]
2022-07-14 killed Safe value. WE ARE NO LONGER SAFE 😬
    [adx.py, bme.py, lsm.py]
2022-07-14 blackbox, altitude error handling
    [rocketData.py]
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2022-07-16 simplified code and patched bugs in phases functions
    [flight_computer.py]
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2022-07-21 fixed some bugs in lsm.py
    [lsm.py]
2022-07-21 fixed bug in main and sensor direction
    [rocketData.py]
2022-07-21 configurated buzzer to buzz for each individual correct board reding and 4 buzzes for none read
    [flight_computer.py, rocketData.py]
2022-07-21 Changed pins to reflect their current uses, added MOSFET for buzzer
    [Xenia-1-rocket-schematic.sch.kicad_pcb, Xenia-1-rocket-schematic.sch.kicad_sch, untitled.kicad_sch]
2022-07-21 Implemented Kris' changes/ fixed bugs
    [HX711Multi.py, adx.py, bme.py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]
2022-07-21 Messed up last commit, hopefully this fixes it.
    [Xenia-1-rocket-schematic.sch.kicad_pcb, Xenia-1-rocket-schematic.sch.kicad_sch, untitled.kicad_sch]
2022-07-22 Revert "Messed up last commit, hopefully this fixes it."
    This reverts commit 25f7ada287da779dced91784588c102a0c06e74c.
    [Xenia-1-rocket-schematic.sch.kicad_pcb, Xenia-1-rocket-schematic.sch.kicad_sch, untitled.kicad_sch]
2022-07-22 Revert "Implemented Kris' changes/ fixed bugs"
    This reverts commit ecdcf5316c69a5beb550738128e959585b0695ed.
    [HX711Multi.py, adx.py, bme.py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]
2022-07-22 fixed Chris changes for real
    [bme.py, flight_computer.py, lsm.py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]
2022-07-22 fixed sensors, ready to merge?
    [adx.py, bme.py, lsm.py]
2022-07-22 Updated logic errors and other errors
    [adx.py, bme.py, flight_computer.py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]
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2022-07-28 fixed some integration issues
    [flight_computer.py]
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2022-08-03 Revert "Code copied from rpi in room 139"
    This reverts commit 13343a36eb4c2b0906274b826b9a893fff334eeb.
    [Xenia-1-rocket-schematic.sch.kicad_sch, cda_no_airbrakes.csv]
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
